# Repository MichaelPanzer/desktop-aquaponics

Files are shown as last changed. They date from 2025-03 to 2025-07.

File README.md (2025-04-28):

**Disclaimer: This project is still a work in progress. I would appricate feedback and ideas to improve but use at your own risk.**

# Build Instructions

## Frame
1. Materials
    1. 2040 aluminum extrusion [Amazon Link](https://www.amazon.com/GUWANJI-Aluminum-1000mm-European-Engraving/dp/B08BCG1FT9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)
    2. Corner bracket kit with M5 screws and t-nuts [Amazon Link](https://www.amazon.com/Silver-Corner-Bracket-Aluminum-Extrusion/dp/B0F1B1N5N1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)
2. Create the base

    Cut List:

    2x fish length width - 40mm

    2x fish width
    
    The base should be a rectangle that overhangs the fish tank by 20mm on the right and left side. A few mm wider might be preferable as it gives some extra clearance when installing the tank. 

3. Add the vertical supports

    The vertical supports are mounted using the corner brackets and can be any height, just be sure to give enough  space to accommodate all grow beds and lights.

## Grow bed
1. Print both halves of the grow bed (I used 100% infil to avoid leaks but you might be able to get away with less).
2. Glue the bed together with two part epoxy, be sure to apply a liberal amount to the inside in order to avoid leaks.
3. Print the outlet spout and install using 2 m4 screws.
3. Install the COB strip to the bottom of the grow bed with 3 m4 screws.
4. Print the grow bed supports and install them at the height of the bed.
5. Fill the bed with expanded clay pebbles [Amazon Link](https://www.amazon.com/dp/B0CR1S1KM7?ref=ppx_pop_mob_ap_share)

## Electronics
1. Materials
    1. Arduino UNO [Amazon Link](https://www.amazon.com/Arduino-A000066-ARDUINO-UNO-R3/dp/B008GRTSV6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)
    2. Prototype Shield [Amazon Link](https://www.amazon.com/dp/B0BNLFXXGV?ref=ppx_pop_mob_ap_share&th=1)
    3. 5v DC-DC buck converter [Aliexpress Link](https://www.aliexpress.us/item/3256806299955878.html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)
    4. 5v water pump [Aliexpress Link](https://www.aliexpress.us/item/3256805952358877.html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)
    5. 3W led driver module [Amazon Link](https://www.amazon.com/Driver-Constant-Current-Control-Dimming/dp/B0CGVYYLKZ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)
    6. Bridgelux EB Series COB module [Digikey Link](https://www.digikey.com/en/products/detail/bridgelux/BXEB-L0280Z-35E1000-C-B3/7907665)
    7. 1307 RTC Module [Amazon Link](https://www.amazon.com/Ximimark-DS1307-AT24C32-Module-Arduino/dp/B07TVMVDDP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)
    7. Mosfet [Digikey Lin](https://www.digikey.com/en/products/detail/nexperia-usa-inc/PSMN1R2-30YLC-115/2674281)
    8. 270 ohm Resistor
    9. 12k ohm Resistor
    10. 1N4001 Diode
    11. 10nf capacitor 
    8. Power Supply: Use a 19.5v barrel-styple laptop charger with appropriate current for the amount of LED modules. 19.5v is pretty common for laptop chargers so you should be able to source something used for cheap. A usb-c pd charger will not work as it relies on communication between the charger and device to determine power level. 
    9. MISC - strip pins, 20-26 ga solid core wire, dupont connectors
2. Solder the components to create the circuit shown in the diagram. (DIAGRAM TO BE ADDED LATER)

## Final assembly

1. Install the shield on the Arduino UNO and mount to the frame
2. Wire the pump, COB strips, and power supply to the circuit
3. Configure the arduino program
    1. Modify the timePoints array to create the lighting profile. Over the course of the day, the intensity of the light will be linearly interpolated between the specified points. 
    2. Configure the on and off timing of the pump.
    3. Flash the firmware to the arduino

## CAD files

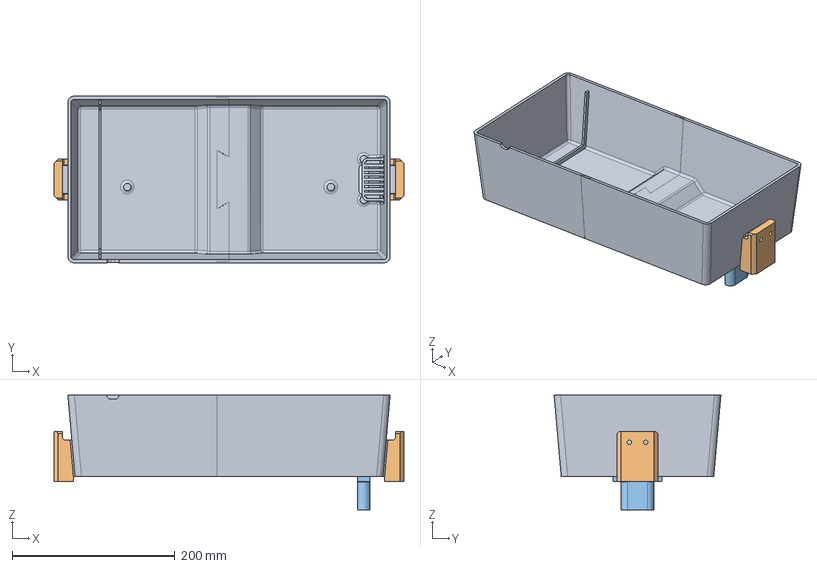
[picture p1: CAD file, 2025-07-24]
cads/Grow_Bed.FCStd
430.0 x 205.0 x 141.0 mm
grow_bed
frame mount
outlet_spout

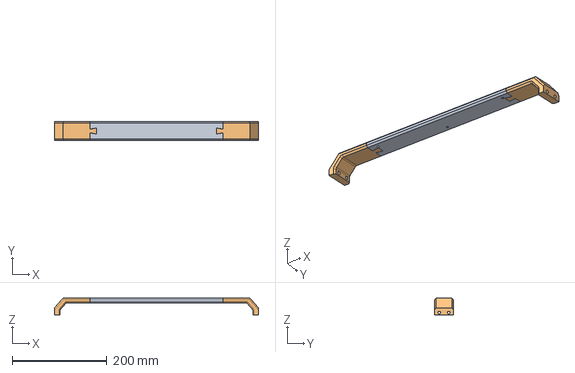
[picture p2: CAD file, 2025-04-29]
cads/light_bar.FCStd
430.0 x 40.0 x 35.5 mm
main bar
side mount

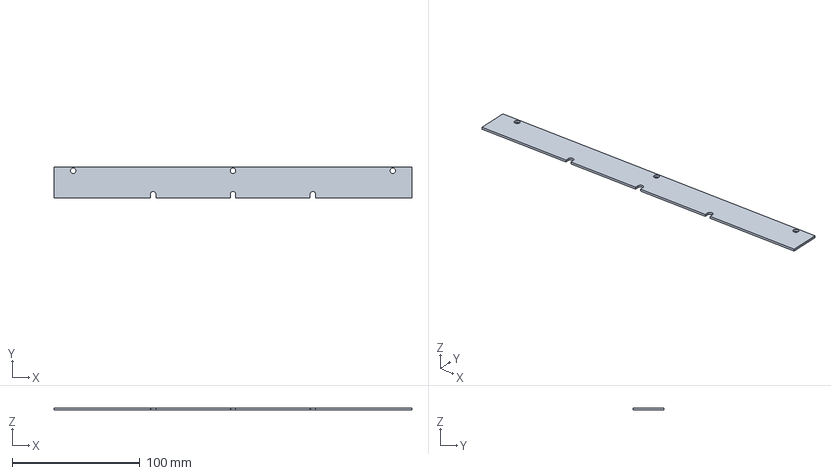
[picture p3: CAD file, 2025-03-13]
cads/280mm_led.FCStd
280.0 x 24.0 x 1.60 mm

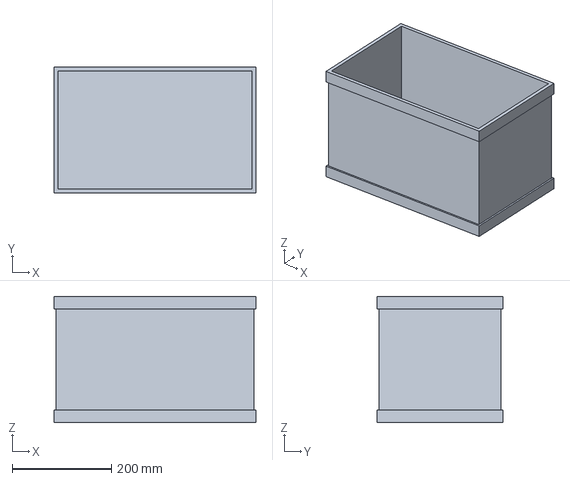
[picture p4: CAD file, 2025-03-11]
cads/Tank.FCStd
406.4 x 254.0 x 254.0 mm

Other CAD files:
cads/grow_bed_asm.FCStd

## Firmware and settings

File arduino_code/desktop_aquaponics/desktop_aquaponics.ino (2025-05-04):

#include "RTClib.h"
#include "TimePoint.h"

RTC_DS1307 rtc;

//Pin assignments
uint8_t tankLight = 3;      
uint8_t bedLight = 5;
uint8_t pump = 11;

//status variables
bool pumpOn = true;
uint32_t previousTime = 0;

//pump timing
uint16_t onTime = 35;
uint16_t offTime = 60;


//TimePoint(hour, minute, intentisy [float from 0.0-1.0])

// Tank lighting profile
TimePoint tankPoints[] = {TimePoint(0,0,0.0), TimePoint(9, 30, 0.0), TimePoint(10, 0, 0.2), TimePoint(14, 30, 0.2), TimePoint(15, 0, 0.9), TimePoint(22, 30, 0.9), TimePoint(23, 30, 0.0)};
uint8_t nT;

//Grow bed lighting profile
TimePoint bedPoints[] = {TimePoint(0,0,0.0), TimePoint(9, 30, 0.0), TimePoint(10, 0, 0.7), TimePoint(22, 30, 0.7), TimePoint(23, 30, 0.0)};
uint8_t nB;

uint8_t intenT, intenB;
uint32_t deltaTime;

//Function linearly interpolates intensity from lighting profile array, returns PWM value of output pin 
uint8_t findIntensity(uint8_t hour, uint8_t min, TimePoint points[], uint8_t n){ 
  TimePoint low = TimePoint(0,-1,0);
  TimePoint high = TimePoint(24,1,0);
  uint16_t totMins = min + 60*hour;

  //set low and high to the TimePoints above and below the current time
  for(uint8_t i=0; i<n; i++){
    if(points[i].getMins() < totMins){//set low 
      if(points[i].getMins() > low.getMins()){
        low = points[i];
      }
    } else if(points[i].getMins() < high.getMins()){ //set high
      high = points[i];
    }
  }

  //Linear interpolation to find the current intensity
  //Comparison is to mitigate 8 bit unsigned integer underflow errors
  if(high.getPWM() < low.getPWM()){
    return low.getPWM() - (low.getPWM()-high.getPWM())*(totMins-low.getMins()) / (high.getMins()-low.getMins());
  } else{
    return low.getPWM() + (high.getPWM()-low.getPWM())*(totMins-low.getMins()) / (high.getMins()-low.getMins());
  }

}

void setup () {
  Serial.begin(9600);

  if (! rtc.begin()) {
    Serial.println("Couldn't find RTC");
    Serial.flush();
    while (1) delay(10);
  }

  //Sets time if rtc not running
  if (! rtc.isrunning()) {
    Serial.println("RTC is NOT running, let's set the time!");
    // When time needs to be set on a new device, or after a power loss, the
    // following line sets the RTC to the date & time this sketch was compiled
    rtc.adjust(DateTime(F(__DATE__), F(__TIME__)));
    // This line sets the RTC with an explicit date & time, for example to set
    // January 21, 2014 at 3am you would call:
    // rtc.adjust(DateTime(2014, 1, 21, 3, 0, 0));
  }

  //Calculate the length of lighting proile arrays
  nT = sizeof(tankPoints) / sizeof(tankPoints[0]);
  nB = sizeof(bedPoints) / sizeof(bedPoints[0]);

  //Define pins
  pinMode(tankLight, OUTPUT);
  pinMode(bedLight, OUTPUT);
  pinMode(pump, OUTPUT);
}

void loop () {
  // Get the current time from the RTC
  DateTime now = rtc.now();

  //Set light intenisty
  intenT = findIntensity(now.hour(), now.minute(), tankPoints, nT);
  analogWrite(tankLight, intenT);
  intenB = findIntensity(now.hour(), now.minute(), bedPoints, nB);
  analogWrite(bedLight, intenB);

  Serial.print("hour :");
  Serial.print(now.hour());
  Serial.print(", minute: ");
  Serial.print(now.minute());
  Serial.print(", tank light: ");
  Serial.print(intenT);
  Serial.print(", bed light: ");
  Serial.print(intenB);

  //Set pump status
  deltaTime = now.unixtime()-previousTime;
  Serial.print(", delta time: ");
  Serial.print(deltaTime);

  if(pumpOn == true && deltaTime > onTime){
    pumpOn = false;
    previousTime = now.unixtime();
    digitalWrite(pump, LOW);
  } else if(pumpOn == false && deltaTime > offTime){
    pumpOn = true;
    previousTime = now.unixtime();
    digitalWrite(pump, HIGH);
  } 

  Serial.print(", pump on: ");
  Serial.println(pumpOn);

  delay(1000);
}

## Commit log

2025-03-11 add cad files
    [Grow_Bed.FCStd, Tank.FCStd]
2025-03-12 add led cad
    [280mm_led.FCStd]
2025-03-13 add outlet features
    [Grow_Bed.FCStd]
2025-03-13 add led strip
    [280mm_led.FCStd]
2025-03-14 add filter
    [Grow_Bed.FCStd]
2025-03-25 shrunk outlet size
    [Grow_Bed.FCStd]
2025-03-28 updated grow bed dimensions
    [Grow_Bed.FCStd]
2025-04-02 Added frame mounting brackets
    [Grow_Bed.FCStd]
2025-04-22 Redesigned outlet
    [Grow_Bed.FCStd, grow_bed_asm.FCStd]
2025-04-22 Added test arduino code
2025-04-24 Fixed Lighting Profiles
    [Grow_Bed.FCStd, light_bar.FCStd]
2025-04-27 added accurate pump control
2025-04-27 added two stage outlet
    [Grow_Bed.FCStd]
2025-04-27 fixed light bar clearances
    [light_bar.FCStd]
2025-04-28 updated arduino code
    [Grow_Bed.FCStd, light_bar.FCStd]
2025-04-28 adjusted outlet dimensions
    [Grow_Bed.FCStd]
2025-04-28 added second light to arduino sketch
2025-04-29 Updated pump timing
    [Grow_Bed.FCStd, light_bar.FCStd]
2025-05-04 Fixed underflow error in linear interpolation
    [desktop_aquaponics.ino]
2025-07-24 updated grow bed
    [Grow_Bed.FCStd]
